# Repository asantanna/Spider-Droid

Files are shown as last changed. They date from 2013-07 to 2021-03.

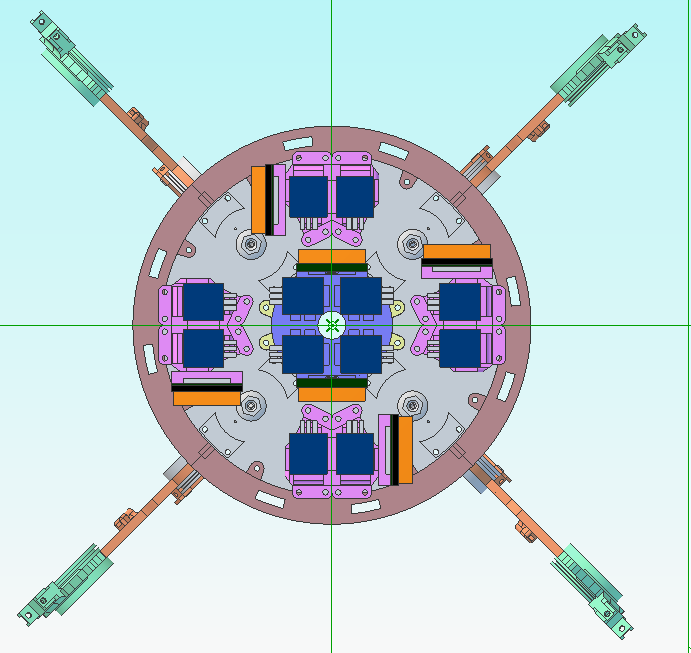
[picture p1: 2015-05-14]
Docs/Raw pics for documents/Phi - Top - Mechanicals Hidden.png

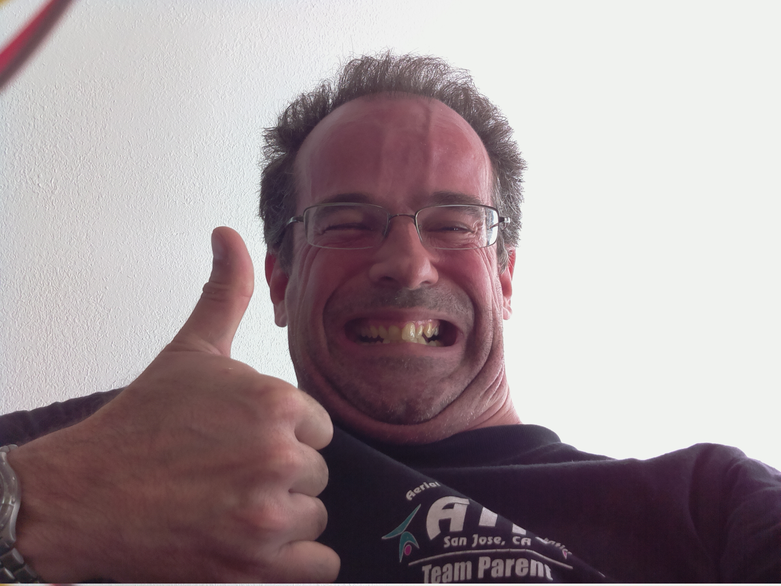
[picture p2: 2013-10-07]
Software/firmware/test/test.jpg

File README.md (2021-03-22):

Spider-Droid
============

Spider like robot - WORK IN PROGRESS

(THIS IS OBSOLETE - COMPLETE RE-IMPLEMENTATION STARTED)

Sparse Checkout
===============

On Raspberry Pi, it is useful to not have to clone this entire repository
since we only need the firmware.  The other stuff will get pretty big and
take up space needlessly.

To set up for this "sparse checkout", create the directory "Spider-Droid"
somewhere on the RPi and copy the file "do-sparse-checkout" into it. (Use
cut & paste or whatever it takes.)

On RPi, look in file for additional instructions.

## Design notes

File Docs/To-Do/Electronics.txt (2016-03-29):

TO DO LIST FOR ELECTRONICS ITEMS
================================

- Aux board does not mount properly on RPi because of video connector clearance
    - remove video connector

- 5V regulator gets very hot
    - install heat sink

- Design touch sensors

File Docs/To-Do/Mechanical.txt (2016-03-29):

TO DO LIST FOR MECHANICAL ITEMS
===============================

BIG AND SMALL SPINDLE:

  DONE *******************- Too much play between spindle and arm, possibly with 
  DONE *******************   spindle and hip limb too

  DONE *******************     INFO: Changes must occur in SPINDLE and BIG SPINDLE to make
  DONE *******************           them thicker.  The alternative, to change the SPINDLE ARM,
  DONE *******************           and RE-MERGE to create SMALL CAP and BIG CAP and the further
  DONE *******************           MERGE to create various other parts is WAY too complicated.

  DONE *******************    SOL: 
  DONE *******************     - Add 0.2 to DIAMETER of hexagon in "SPINDLE" and "BIG SPINDLE"
  DONE *******************     - ignore now incorrect REF sketch in "SPINDLE ARM"

  ******* NOTE *****
  This may make the bearing more snug ... we may need to tweak it back with a revolution "shave"
  if necessary. It's hacky but it's the easiest thing to do BY FAR.

CABLE TUBE SUPPORT:

  DONE ******************* - Need widen hole in cable tube supports
  DONE *******************     SOL: maybe add 0.2 to DIAMETER of hole for glue space too

FRAME:

  DONE *******************- Motor driver support is bad - gap is too thin, holes are two big
  DONE *******************    SOL:
  DONE *******************      - remeasure controller board to see why this happened
  DONE *******************      - change "slot" for driver board to single tabs
  DONE *******************      - figure out what to do about the screws ... I think the holes
  DONE *******************        are too tiny for any of the screws we have.  Try to come up
  DONE *******************        with something clever so we don't need a new screw type.

  DONE ******************* - Need two cable supports for motor wires that go to other frames

  - Need to plan path of motor wires to see where they go and if it will work

  DONE *******************- Paperclip that limits spindle arm is wonky.
  DONE *******************    SOL: 
  DONE *******************      - Add hole to frame to have arm stopper hole go all the way through to other side
  DONE *******************      - Modify stopper hole arrangement so paperclip is more sturdily held in place.
  DONE *******************        (see post-its)

MINI-POT:

  DONE ******************* - Position of threaded hole is incorrect
       *******************   - SOL: fix but must also fix pot base support afterwards

POT BASE SUPPORT:

  DONE ******************* - change to mini-pot invalidates some things
       *******************   - SOL: reproject REF figures, fix hole, fix ridges

=============================================================================

FUTURE
======

- Figure out where RPi, accel, gyro and hip controller attach

- Design touch sensor mechanicals

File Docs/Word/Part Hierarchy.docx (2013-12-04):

Phi Spider Droid Part/Assembly Hierarchy:

(A) = Assembly
(P) = Part

- Phi (A)
  - Head (A)
    - Head Dome (P)
    - Gyroscope (P)
    - On/Off Switch (P)
    - Battery (P)
    - LEDs (P)
  - Main (A)
    - Logic Unit (A)
      - Board Mount (P)
      - Raspberry Pi (P)
      - Phi Logic (P)
    - Hip Unit (A)
      - Hip Motor Mount (P)
      - Pot Mount (P)
      - Hip Motor (P) x 4
      - Pulley x 4 (P)
    - Leg Frame (P) x 4
    - Leg Unit (A) x 4
      - Leg Control (A)
        - Motor Mount (P)
        - Pot Mount (P)
        - Bearing Mount (P)
        - Motor Controller (P)
        - Motor (P) x 2
        - Pot (P) x 2
      - Leg (A)
        - Hip (P)
        - Thigh (P)
        - Shin (P)
      - Pulley – Thigh (P)
      - Pulley – Shin (P)
  - Skirt (P)

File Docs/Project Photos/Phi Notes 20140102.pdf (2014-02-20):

## PHI Project Notes

Overview

The name of the robot is PHI because, as everybody knows, Greek letters are COOL.

It is loosely based on the Star Wars Spider Droid. Loosely because after close inspection, I concluded it wouldnt work There are linkages missing, etc unless they use light saber technology or something.

Software

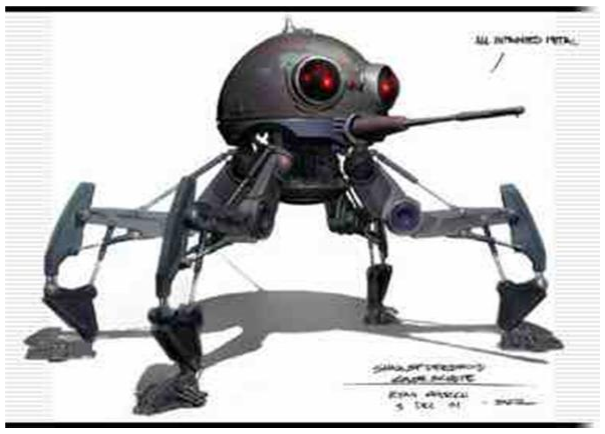
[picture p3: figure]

The software is broken into two parts:

1) Firmware (on robot)
a. Hardware Control (sensors and effectors)
b. Web server for diagnostics
c. PhiLink (50 fps telemetry link)
2) Phi Core (on Windows PC)
a. Remote brain for robot robot is teleoperated like a puppet through PhiLink. At this point it is mostly WISHFUL THINKING. Only diagnostics and telemetry work.
b. Self-programmed guided by hardwired instincts and goals
i. Instincts are things I presume comes wired in out of the egg. Things like pleasure seeking, pain aversion, curiosity, investigation, prediction, play, feeling in control, etc
ii. Goals are loose good/bad indicators that guide learning. Similar to instincts but less fuzzy. E.g. at a very low level, a goal of the low joint sensor/motor subsystem is to explore the causality between motor commands and joint movements. This is how Phi learns it has a leg.
iii. Self-programming is based on various information-theoretic goals. 1. Maximal communication entropy between systems (ie best channel

utilization)
2. Maximal PIG (predicted information gain). This means that exploration actions are selected on the basis of filling in missing knowledge relevant to the goal.
3. Best compression between sensor and memory by the information bottleneck method. Lots of data from sensors but very little is relevant to a particular subsystem. Subsystems compress (and discard) data that is not relevant to its goal. In other words, information goes through a bottleneck.

Hardware

Quick summary:

- Raspberry Pi single board computer running Raspbian Linux (derived from Debian) - Auxiliary custom PCB for: Voltage regulators , Analog-to-Digital converters, SPI and I2C bus

expanders, etc. - 12 gear motors (35:1 ratio), 3 per leg

- 6 motor controllers (one can handle 2 motors) - 12 Potentiometer based joint position sensors, 3 per leg
- 4 touch sensors on feet
- Static Accelerometer senses acceleration on 3 axes. Good for detecting translational movement of robot
- Digital Gyroscope senses rotational acceleration around 3 axes. Good for detecting robot rotations. - 50 fps HD camera (resolution will probably be reduced significantly to keep frame rate up) - 2400 mAh 9V batteries
- 9V for motors
- 5V for Raspberry Pi
- 3.3V for assorted logic
- On/off switches and assorted blinkenlights

Plastic

View of one Quadrant of robot. Phi is made of four of these, a head dome and an undercarriage dome.

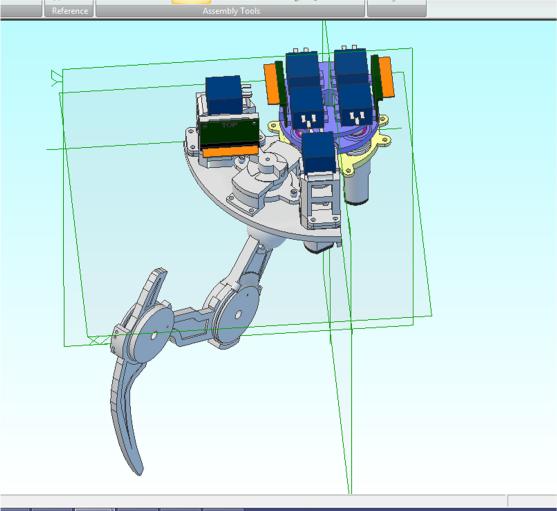
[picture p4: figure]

Side view of a Quadrant:

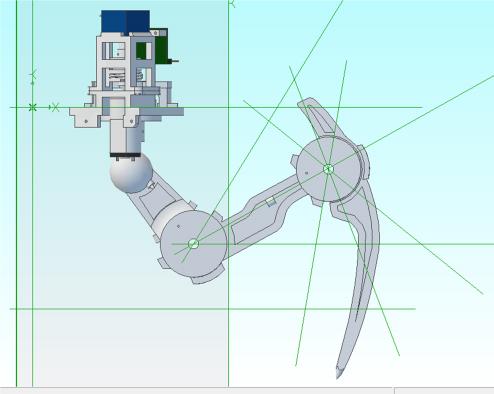
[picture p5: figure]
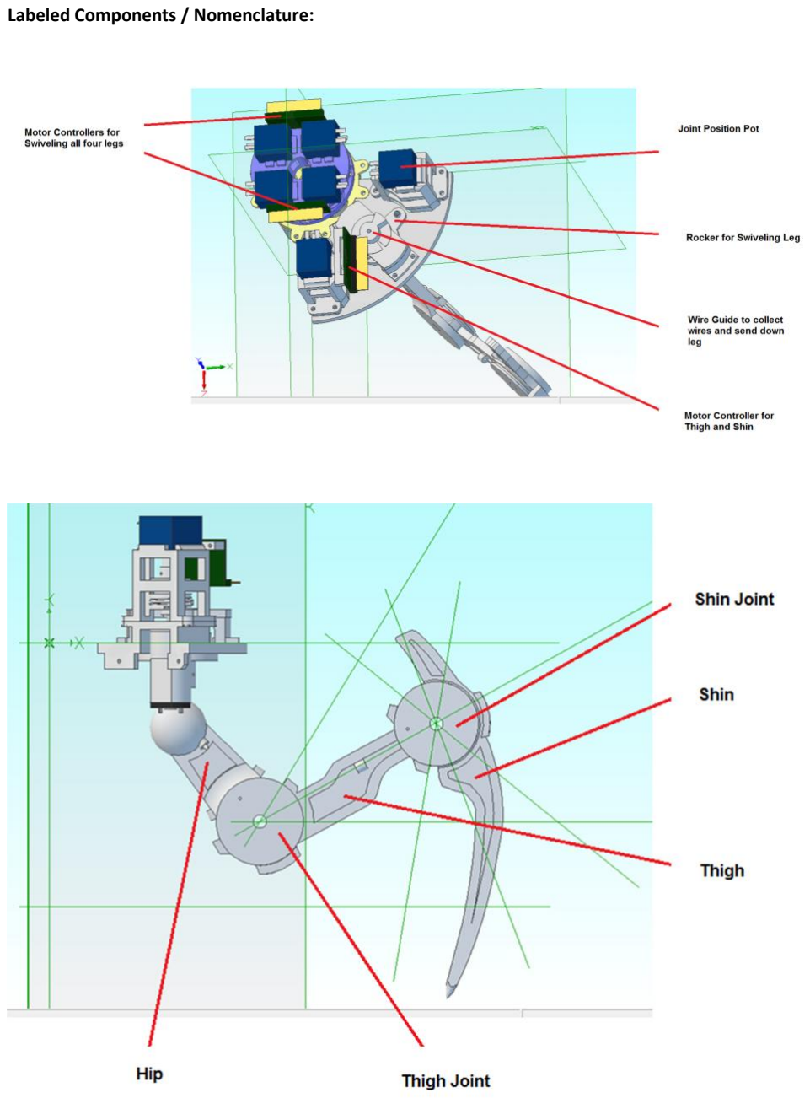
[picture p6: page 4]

Labeled Components / Nomenclature:

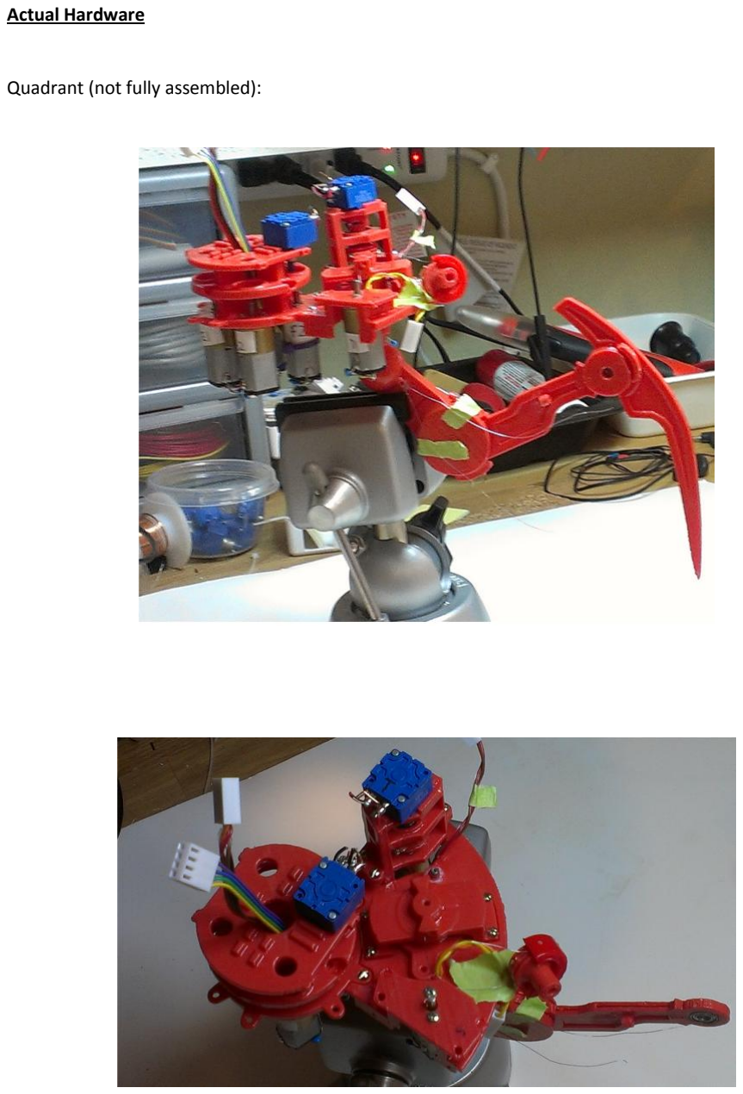
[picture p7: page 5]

Actual Hardware

Quadrant (not fully assembled):

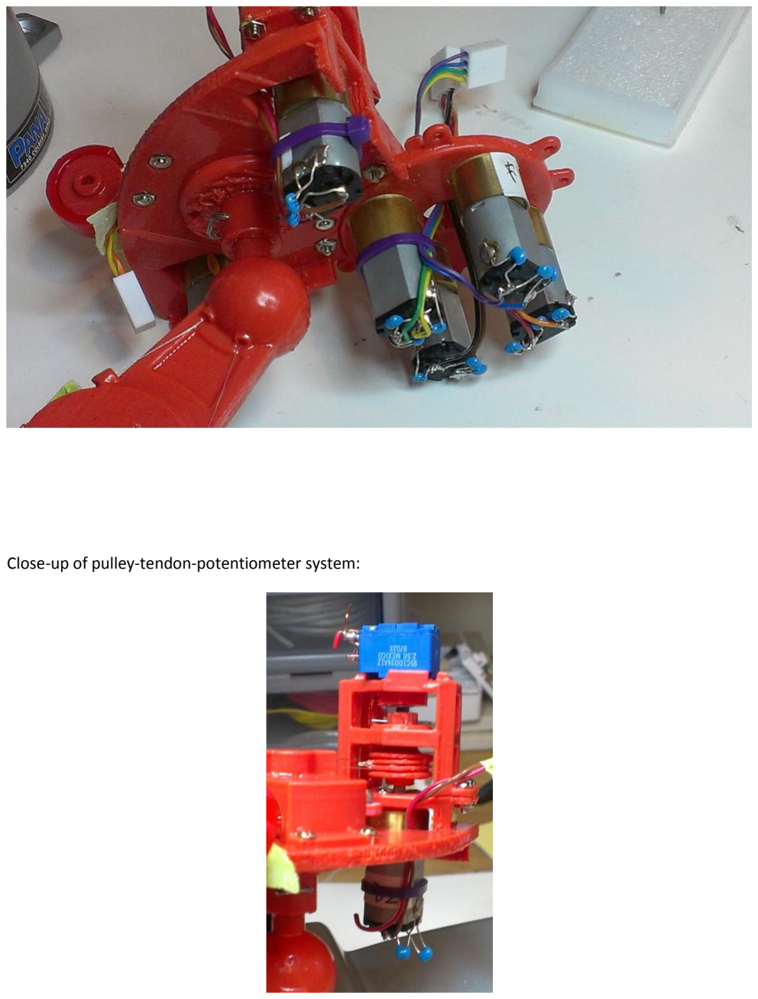
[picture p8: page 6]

Close-up of pulley-tendon-potentiometer system:

Aux Board

Top:

Bottom:

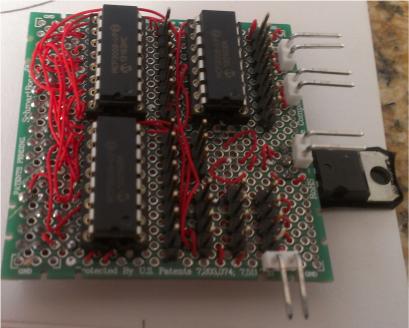
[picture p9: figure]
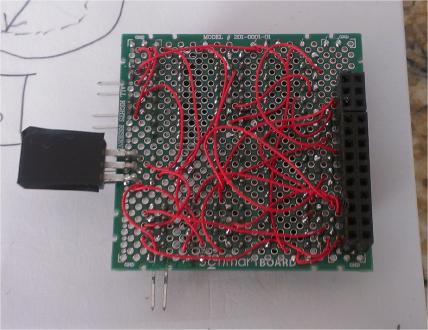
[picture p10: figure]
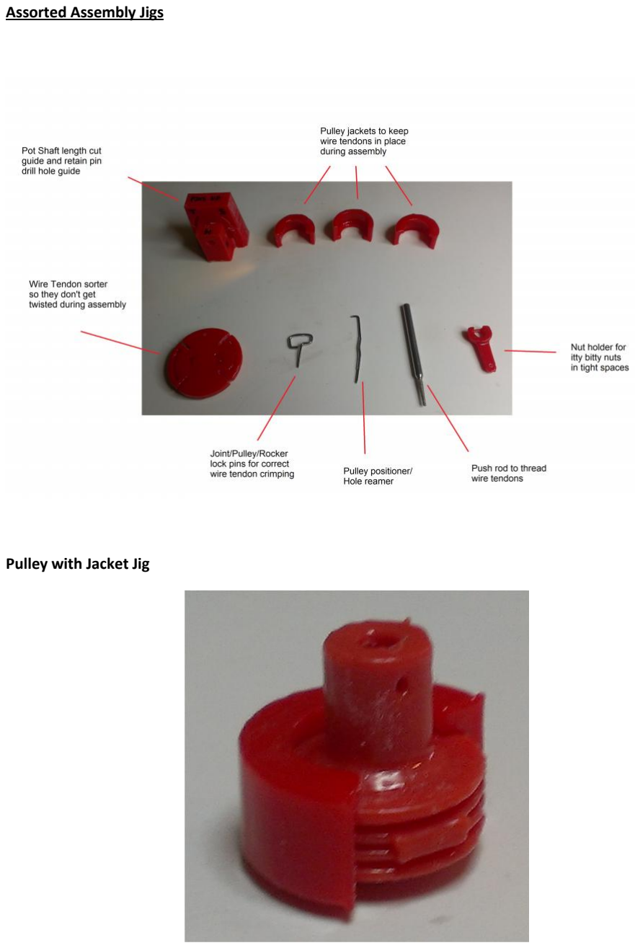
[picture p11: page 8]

Assorted Assembly Jigs

Pulley with Jacket Jig

Most Important

Project Mascot (weird Egyptian God)

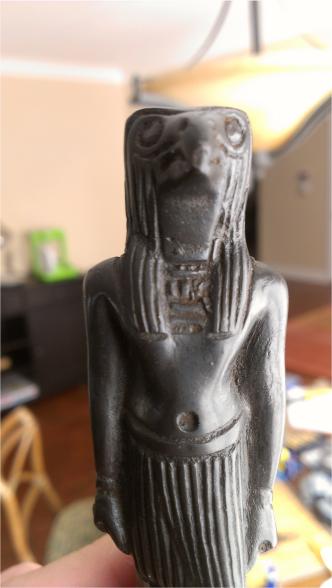
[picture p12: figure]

Keychain (no mugs or T-shirts yet)

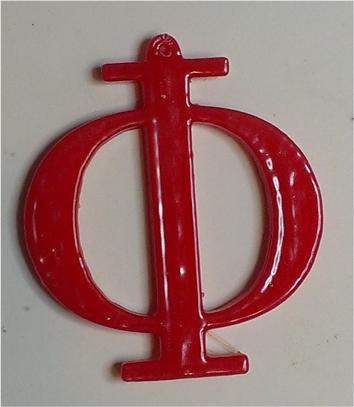
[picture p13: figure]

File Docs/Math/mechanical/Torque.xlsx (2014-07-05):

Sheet: Calculations
Motor Torque Calculations |  |  | * see note 1
 | Motor Type: | Polulu 1598 | g / oz | 28.35
 | Gear Ratio: | 115 : 1 | mm / in | 25.40
 | Stall Torque (oz-in) | 35.00 | Pulley Rotation (turns) | 0.75
Inputs | Motor Pulley Radius (mm) | 6.50 | * see note 2
 | Joint Pulley Radius (mm) | 15.00 | * see note 3
 | Limb Length (mm) | 76.42 | * see note 4
Intermediate | Stall Torque (gf-mm) | 25202.71 | Mot Pulley Circum (mm) | 40.84 | hypothenuse (mm) | 15.00
 | Wire Tension (gf) | 3877.34 | Wire Travel (mm) | 30.63 | base (mm) | 15.32
 | Leg Torque (gf-mm) | 58160.09 | Attach Pt Circum (mm) | 94.25
Results | Endpoint Force (gmf) | 761.08
 | Wrap Leg Rotation (deg) | 117.00 | if attached like a pulley (wrapping)
 | Lever Leg Rotation (deg) | #NUM! | if attached to a lever (with symmetric movement)
Design Decisions | THIGH |  | SHIN
 | Motor Pulley Radius (mm) | 6.50 | Motor Pulley Radius (mm) | 6.50
 | Joint Pulley Radius (mm) | 30.00 | Joint Pulley Radius (mm) | 29.00
 | Limb Length (mm) | 76.42 | Limb Length (mm) | 103.93
 | Wrap Leg Rotation (deg) | 58.50 | Wrap Leg Rotation (deg) | 60.52
 | Endpoint Force (gmf) | 565.37 | Endpoint Force (gmf) | 401.86
Notes:
1) This worksheet computes a *single* joint at a time. The Design decisions at bottom are cut/paste of values for different joints.
2) The motor pulley radius is self-explanatory.
3) The joint pulley radius is equivalent to the radius of the "other" pulley - the one at the joint. When there is no pulley, just a lever arm like the hip rocker, it is the length of the arm.
4) The limb length is the length of the limb being moved. This length is the joint-to-joint straight distance. For the thigh, it is the distance between bearing centers. For the shin, it is the distance from the center of the bearing to the contact point.

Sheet: Polulu Motor Data
Motor Type: | Polulu 1795
Gear Ratio: | 35 : 1
Stall Torque (oz-in) | 13.00
Motor Type: | Polulu 1598
Gear Ratio: | 115 : 1
Stall Torque (oz-in) | 35.00

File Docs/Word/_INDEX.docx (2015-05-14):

PHI Index

Mind/Memory Hierarchy

Concepts

Noise

States & Change

Mind/Memory Hierarchy

It seems reasonable that:

- Big concepts are built of smaller ones.
- Information is not endlessly repeated so the same datum/concept is not duplicated in every concept/memory that refers to it. In other words, concepts are referenced with something like pointers.

However, this leads to several consequences:

- If a concept changes, then anything referencing it will also change.
- If the change is small, perhaps this does not have great consequences.
- If , however, the change in the concept is big, or if it becomes invalid, then the concepts/memories that reference it either become incorrect or end up having what is in effect a dangling pointer – ie a reference to a no longer existent concept.
- We can think of the concept hierarchy as a building where “foundation concepts” form the base and new concepts are built on top. Modifying the base can cause large quakes in the whole structure.

Is this reflected in what we know about memory development?

When the system has very little experience, there isn’t much that already exists and can be properly considered to be foundational data. This means that structures built are quite likely to be built incorrectly (strange/useless concepts, weird/crazy causality, overly convoluted organizations, very little generalization, etc.) and that these “uneducated” systems will inevitably be subjected to deep revisions as time goes by and “refereeing data” invalidates previous concepts.

This is inevitable:

1) A core of experience must be acquired in order to properly create/organize concepts correctly/usefully. In the beginning, there will not be enough history to do so and things will very likely be messy.
2) Since concepts are continually being built on other concepts and memories are continually being built referring to whatever concepts we currently have on hand, a structure with shaky foundations will be built at first.

Concrete Consequences:

Since the less experience a system has, the more malleable are its foundations, then “younger” systems will not be able to “remember” as far back as a more experienced system. The concepts that form memories in young systems will get invalidated much more often and these memories will cease to make as much sense. When the concept changes are small, the invalidated concepts might cause only a fuzzy memory to remain. When the change is big, the memory might be sufficiently damaged so as to make it terminally invalidated. These probably get discarded or simply wither away through some auxiliary mechanism.

This also provides a more palatable alternative to the idea that we have hardwired phases of development such as strict hardwired learning windows. Instead:

1) We would explain the beginning of a learning window as the (fuzzy) point in time where a sufficiently reliable foundation exists on which to build a particular type of concept. Before this point, either the necessary base concepts do not exist or are in flux, preventing the formation of a solid and persistent new concept.
2) Similarly, the end of a learning phase is not “genetically preprogrammed” but is instead a consequence of the foundations firming up as its concepts become more established and entrenched through verification. Presumably a mechanism exists where a heavily verified and/or relied upon concept is not easily changed as something that is new and/or untried.

Anecdotal Evidence:

1) By observing young children, 8 year-olds, 12-year olds, etc. It is readily apparent that they have *very* good memories. There is nothing wrong with their ability to form memories that are precise and robust. Yet, we know that the great majority of these memories will be lost as they grow older. None of us remember much from those years and when we do, not with any great clarity.  This explanation proposes that what happens is that most memories become terminally invalidated and subsequently lost. Memories of deep emotionally significance, for example, might, on the other hand, still retain enough “pointers” to valid base foundational concepts (the emotions themselves) so as to survive – but with likely great lack of clarity since other components of the memory will probably have been invalidated. Potentially, these heavily compromised components are then repaired by the mind by either:
  a. Automatic repair / confabulation (which appears to be rigidly controlled, except when the mind is subjected to very peculiar circumstances such as separated hemispheres or some types of disease or damage)
  b. Conscious replacement / rationalization of what “ought to be there” or “was told was there”
2) In contrast, with older people, we do not see this widespread “wiping out” of whole periods of memory. It is quite common for even very old people to say “they remember that as if it was yesterday” even when referring to events that occurred many decades ago. This explanation proposes that for older people, very large and time tested hierarchies exist at the time of memory formation and that they consequently do not require deep revisions afterwards. Thus the memory is preserved with great clarity.
3) It should be said that this doesn’t mean that older, more experienced people will therefore remember everything. Instead, what is being said is that if other mechanisms mark a memory as worth remembering, it will last longer and retain greater clarity for these more experienced people due to the stability of their mental hierarchy. (We are of course referring to healthy people – at advanced ages, senility may cause the system to malfunction in a variety of ways – in both memory formation and retrieval.)

Consequences to Phi

1) To get the ball rolling, there should probably be some hardwired foundational concepts.
  a. Simple feelings and emotions seem intuitive: pain, hunger, fear, etc.
  b. Maybe all qualia are foundational concepts. However, when we think of color for example, it seems clear that color qualia are not fully hardwired but instead develop over time (but probably very early). Consider that an animal that is born with a mutation that endows it with a new photo-pigment would develop qualia to represent the new colors. Since this happens often throughout evolution with success – it seems that the qualia cannot be fully hardwired because it would be extremely unlikely to have both the mutation for the photo-pigment and a suitable mutation to the hardwiring occurring at the same time.
2) Suitable mathematical mechanisms must be devised to:
  a. Form concepts.
  b. Evaluate the trustworthiness (though validation) and authority (through being relied upon) of concepts
  c. Controlling the ease of modification/invalidation of concepts. (Can concepts be modified or only invalidated and replaced? Or both?)
  d. Recovering from such invalidations both in the concept hierarchy and in memories.

Concepts

It seems intuitive that concepts must be some sort of (exclusive?) categorization of the state and that any concept cannot be always active.

1) If two concepts are indistinguishable, they are logically the same concept
2) If a concept is always active, then it is not useful to base a decision. So concepts must be active only part of the time.
3) Similarly, if a concept is never active, again it is useless.

Concepts and info theory:

1) It follows from the above that with concepts, some sort of information entropy argument should apply. Ideally there should be an equal distribution of the activity of concepts or something.
2) Also, since concepts are categorizations of state, we are often interested in cause and effect between them.
3) This is a bit confusing – if a concept is a categorization of state then it might also be a cause? In which case it’s hard to argue for entropy. For example, if a concept can be a cause and a particular cause might be an event that happens once and has big consequences and should be remembered. This does not seem to have anything to do with entropy.
4) Maybe we need to say something like causes are identified by co-occurrence of concepts. The concepts need to follow entropy arguments – the causes are just episodic memories of cause coincidences?

Noise

With regards to states and concepts, we are always most interested in transitions (changes) between them. The problem is that noise can cause random transitions that cannot be solved by simple discretization.

1) Even with states being categories that are discretized far apart, if the true state of the system is on the border between categories, noise can make them appear to ping-pong back and forth.
2) A mechanism is required to prevent this ping-ponging such as:
  a. Some type of Hysteresis
  b. Some sort of momentum mechanism that keeps the state moving into the new symbol and thus away from the border
  c. Having a “no-man’s land” between states and having a mechanism that generates change events only if the transition is part of a sequence of the form. If the no-man’s land is wide enough, noise will not be able to fully traverse it on its own to enter a new symbol and thus will eventually reenter the same symbol – causing the change to be ignored.

States & Change

1) Changes are the fundamental entities from which any intelligent system is built since, ultimately, only changes can be used to trigger decisions and thus actions (physical or mental) that the system predicts will be beneficial. This follows from the logic that:
  a. If an action is to occur, it must perforce have a cause or decision preceding it to trigger it to begin.
  b. This trigger must occur at a specific moment to have beneficial results.
  c. A “moment” can only be identified if it is different from the moment immediately preceding it in some way.
  d. Thus the change that allows identifying the beginning of a specific moment is THE fundamental entity from which intelligent systems are built.
2) States on the other hand, are related to changes because we can say that a transition from one state to another is what constitutes the change.

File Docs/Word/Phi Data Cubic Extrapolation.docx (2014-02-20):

Phi Data Cubic Extrapolation

A common method for extrapolating (or interpolating) data points is cubic interpolation/extrapolation. Interpolating is when you want to guess a point between some other data points. Extrapolating is when you want to guess a point outside other data points.

Interpolation: Extrapolation:

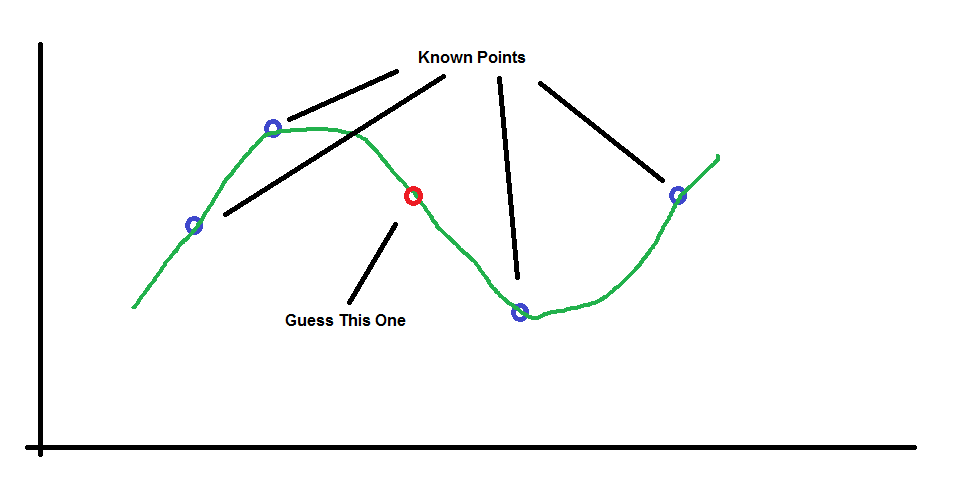
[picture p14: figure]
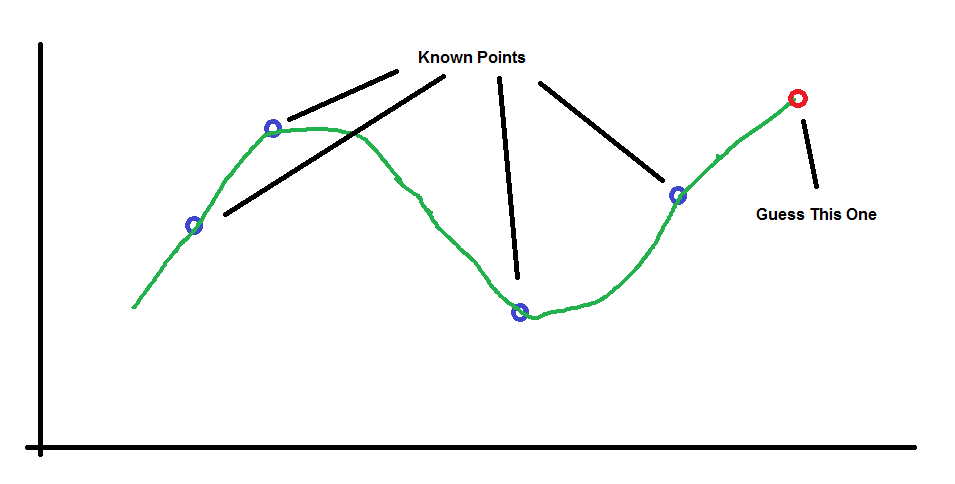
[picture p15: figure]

The problem is that we don’t know the green curves beforehand so it’s actually impossible. However, if we assume a few things that are not too unreasonable, then the problem becomes solvable. We will assume 2 things:

1) The curve is smooth looking – not some crazy hairball type of thing
2) It has at most 2 “bends” – places where it changes direction. In other words, at most 2 reversals from “increasing” to “decreasing” (or vice versa).

A family of curves that meets our requirements is described by what is called a cubic equation. The idea is that we will provide some existing points and assume that they are on a curve that can be described with a cubic equation and ask: “if we know all these points are on a cubic curve, then what is the equation of the curve?”

The general form for any cubic equation is:

Our goal is to determine what the values of a, b, c and d using some example points that we claim are on the cubic equation we want to know. Since we want to solve for 4 values, there’s a mathematical rule that says we need 4 “examples” in order to figure it out. (It will become clear why this is so below.)

So the example points will be:

Thus there are four equations that must be true:

We want to solve for a, b, c and d in general but there is a trick that we can use to make things simpler. The reason we want to solve the cubic equation is because we want to guess a point at some other x value such as x5, but if we shift the points left or right to make sure that the point we want to guess is always at 0, then all we need to solve for is d; the equation for the point we want would then be :

Here’s how to solve it. First solve for a in terms of the others using the first equation:

Matlab answer:

2

b x1 + c x1 + d - y1

3

x1

Now, use this value for a in the second equation to make a go away. Then solve for b.

Matlab answer:

The value of b is:

3

x2 (d - y1 + c x1)

d - y2 + c x2 - -------------------

3

x1

3

x2 2

--- - x2

x1

Now solve for c using the 3rd equation:

Got tired of simplifying … stopped doing it here.

Matlab answer:

The value of c is:

2 2

x2 x3 (y1 - y3) x2 x3 (y1 - y2) x2 x3 (d - y1) (x2 - x3)

2 2 2 2 ---------------- - ---------------- + ------------------------

d x2 - d x3 - x2 y3 + x3 y2 x1 - x3 x1 - x2 x1

2 2 x2 x3 (x2 - x3)

x2 x3 - x2 x3

And FINALLY!!! :

Lucas and I didn’t want to spend the next six hours doing this so we just gave it to Matlab.

Matlab answer:

The value of d is:

2 2 2 2 2 2

- y4 x2 x3 + y3 x2 x4 + y4 x2 x3 - y3 x2 x4 - y2 x3 x4 + y2 x3 x4

2 2 2 2 2 2

- x2 x3 + x2 x4 + x2 x3 - x2 x4 - x3 x4 + x3 x4

x2 x3 x4 (x3 - x4) (y1 - y2) x2 x3 x4 (x2 - x4) (y1 - y3) x2 x3 x4 (x2 - x3) (y1 - y4)

---------------------------- - ---------------------------- + ----------------------------

x1 - x2 x1 - x3 x1 - x4

(x2 - x3) (x2 - x4) (x3 - x4)

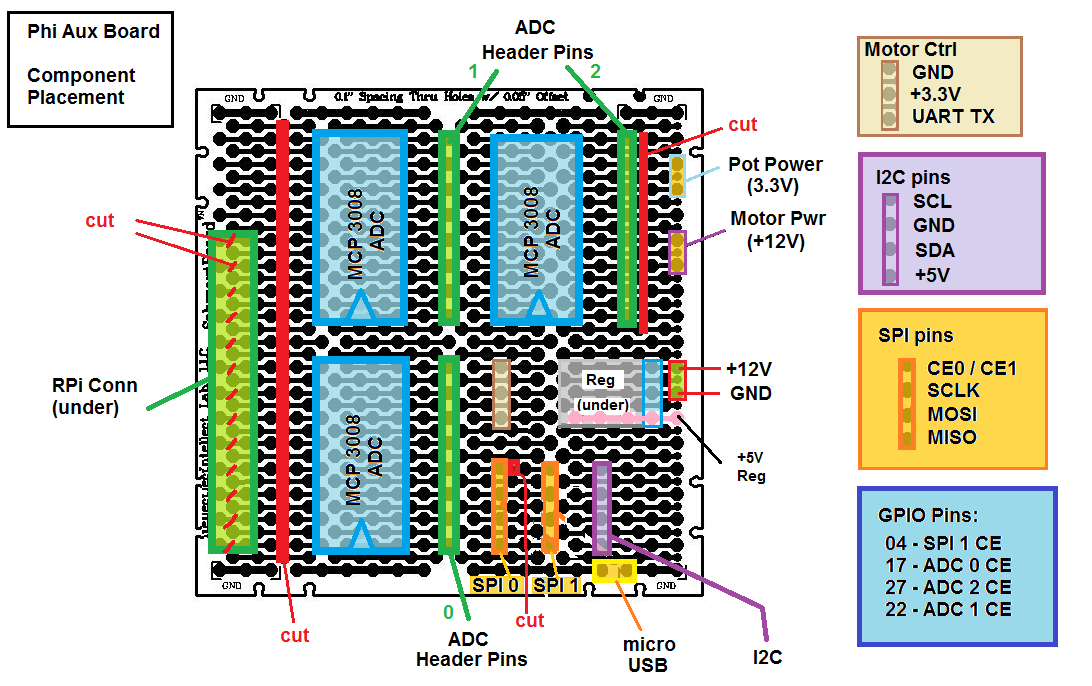
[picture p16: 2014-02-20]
Phi Schematics/Prototype Board/schmart-board-placement.png

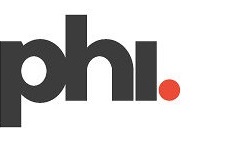
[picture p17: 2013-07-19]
Software/firmware/bin/wwwRoot/images/phi_text.jpg

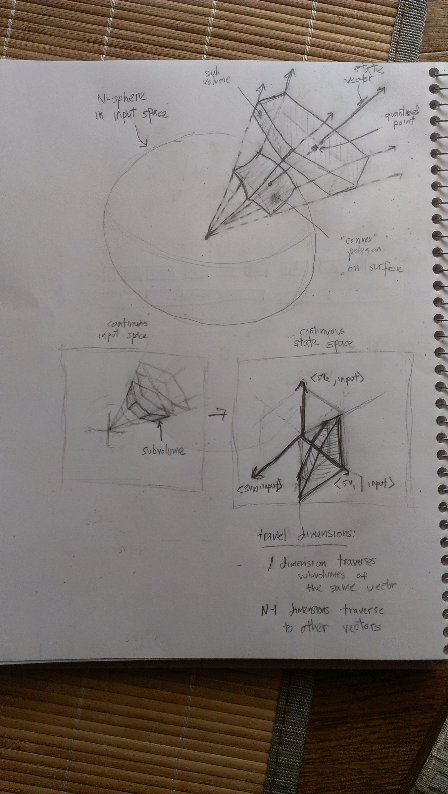
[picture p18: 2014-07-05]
Docs/Raw pics for documents/State spaces.jpg

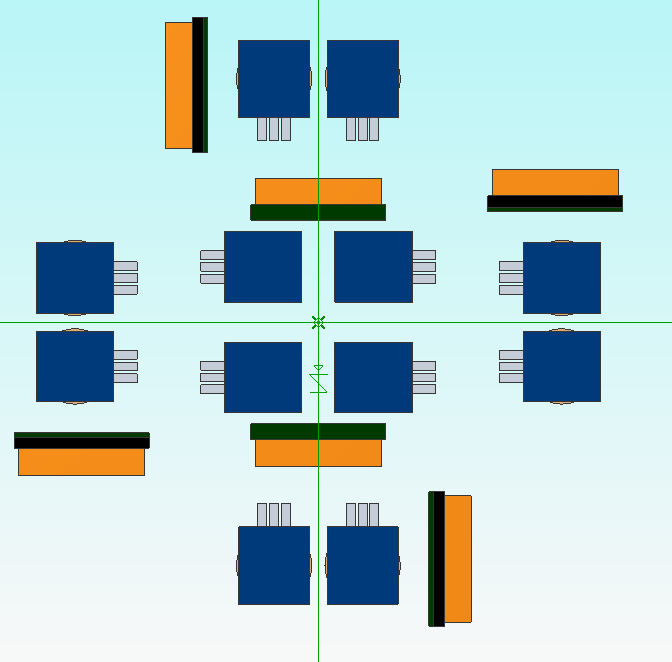
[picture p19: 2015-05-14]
Docs/Raw pics for documents/Phi - Top - Pots & Controllers Only.png

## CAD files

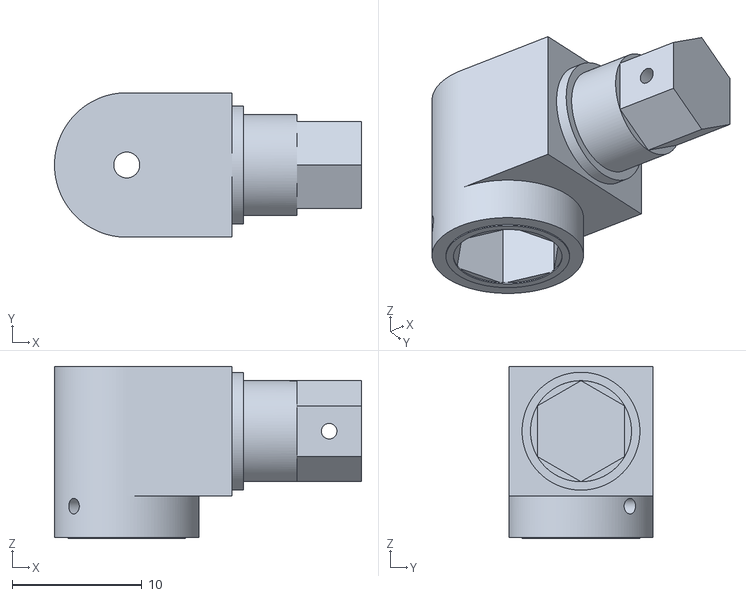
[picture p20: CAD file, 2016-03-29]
GeoMagic/Version 0.3 - Abandoned/STL Files/MERGED - Thigh Arm R.stl
23.7 x 11.2 x 13.3

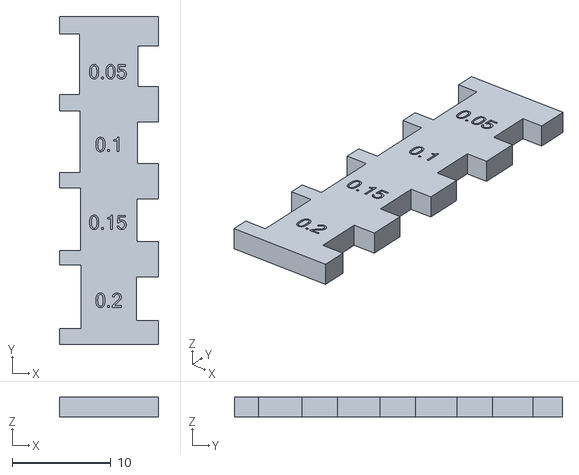
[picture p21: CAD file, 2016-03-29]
GeoMagic/Version 0.4/STL Files/Clearance Notches.stl
10.0 x 33.2 x 2.00

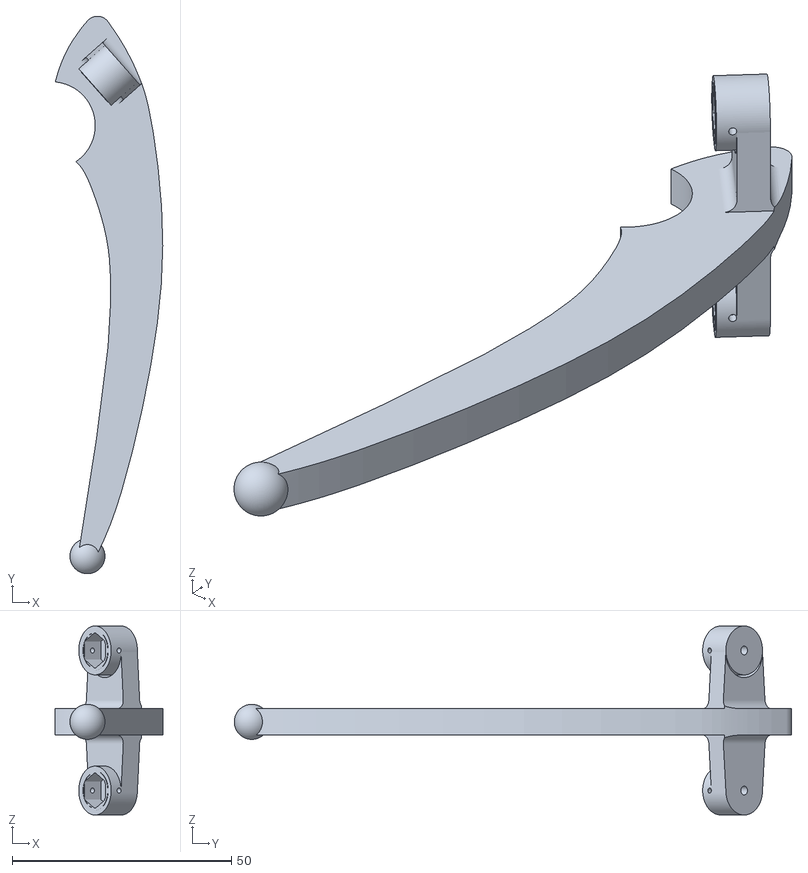
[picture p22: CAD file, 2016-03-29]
GeoMagic/Version 0.3 - Abandoned/STL Files/MERGED - Shin Limb.stl
24.5 x 127.2 x 43.1

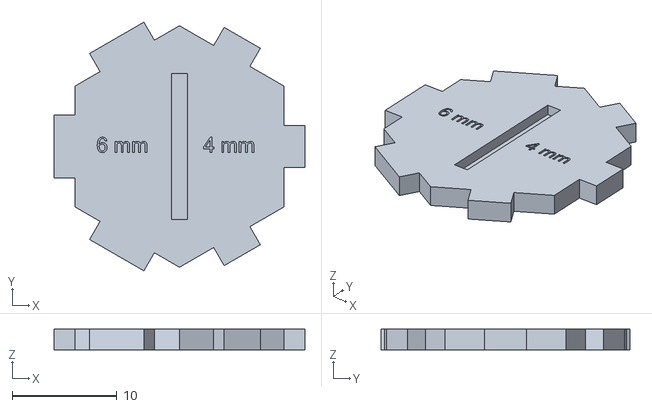
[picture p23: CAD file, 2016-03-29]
GeoMagic/Version 0.4/STL Files/Clearance Notches B.stl
24.0 x 23.8 x 2.00

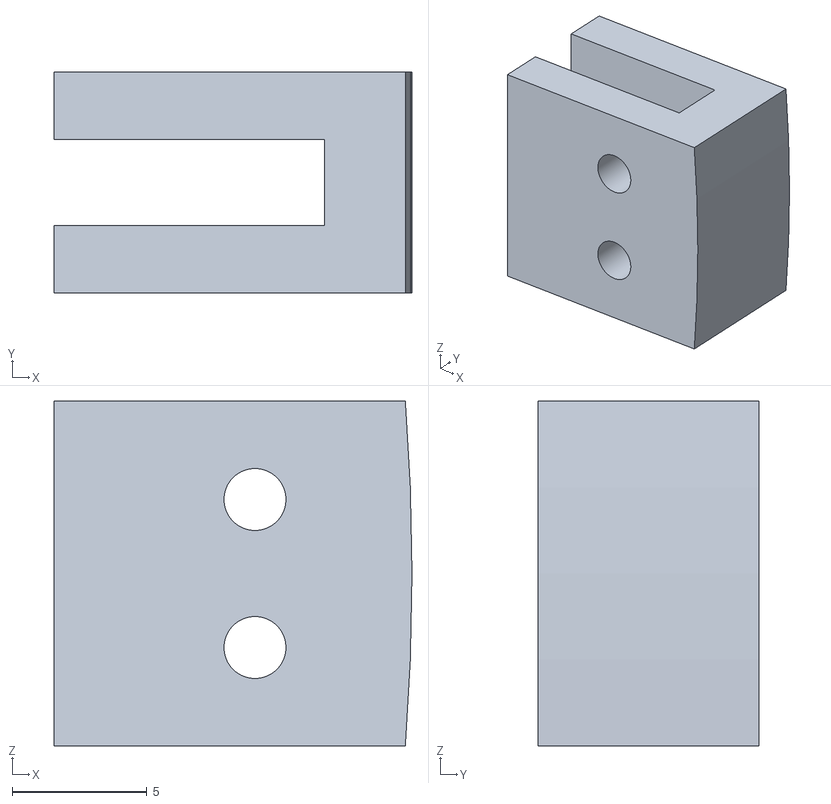
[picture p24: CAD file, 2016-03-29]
GeoMagic/Version 0.3 - Abandoned/STL Files/Outer Frame Clip.stl
13.3 x 8.20 x 12.8

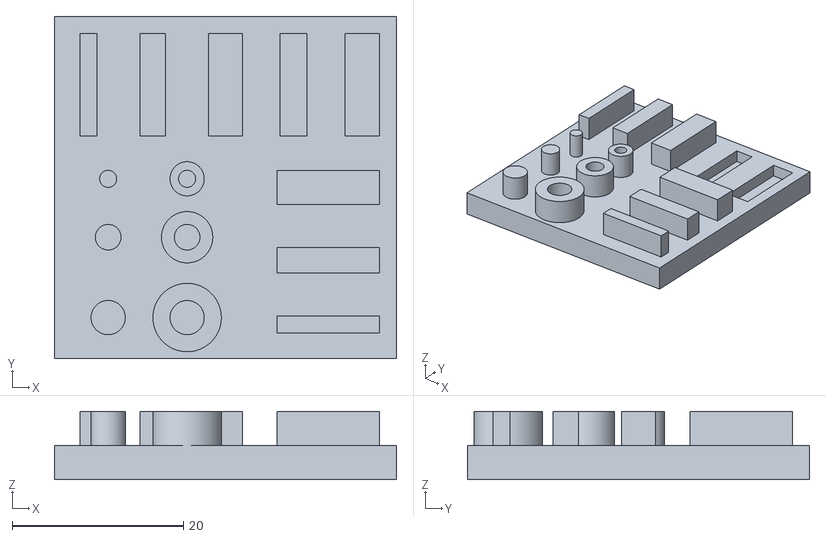
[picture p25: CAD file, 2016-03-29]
GeoMagic/Version 0.4/STL Files/Lines and Circles Calib.stl
40.0 x 40.0 x 8.00

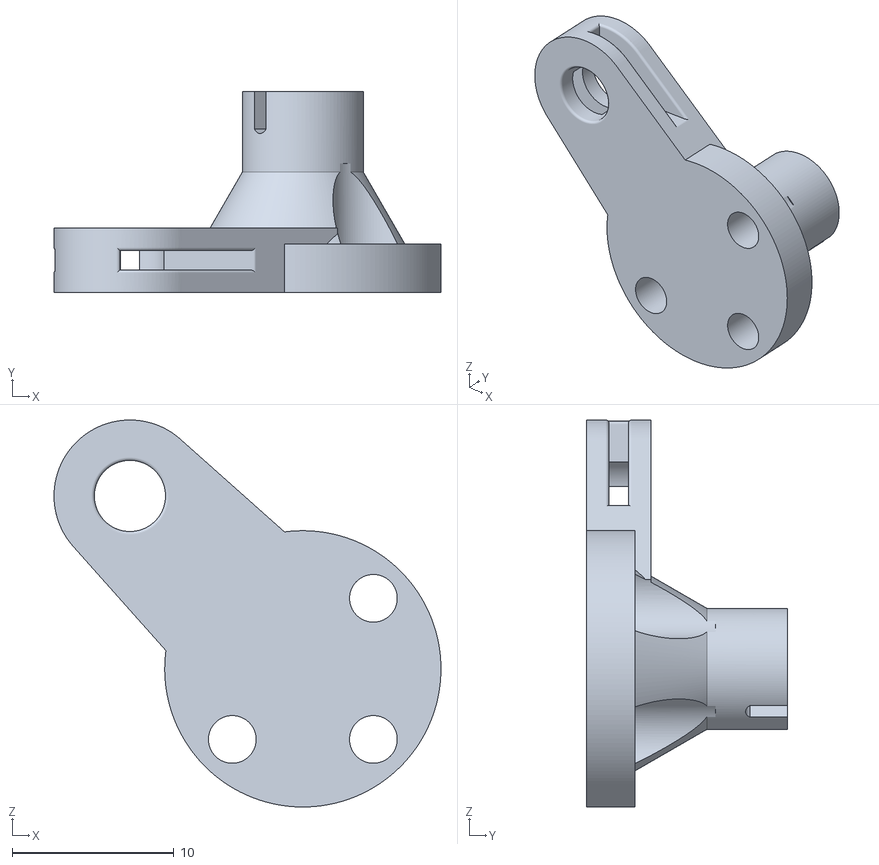
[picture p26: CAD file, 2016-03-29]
GeoMagic/Version 0.3 - Abandoned/STL Files/MERGED - Hub Arm.stl
23.9 x 12.4 x 23.9

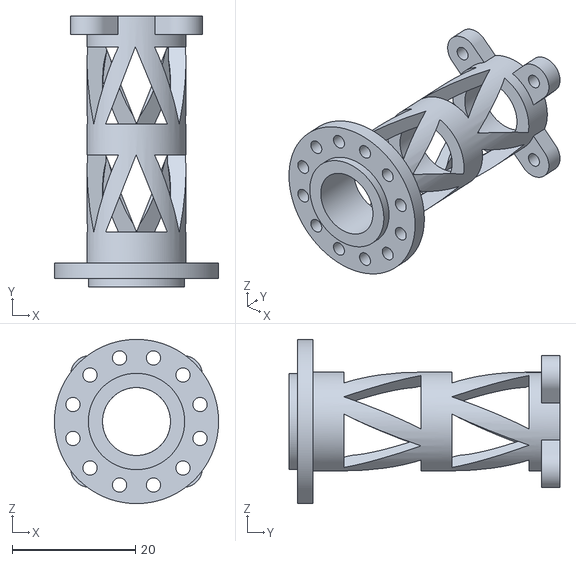
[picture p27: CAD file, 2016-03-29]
GeoMagic/Version 0.3 - Abandoned/STL Files/Tower.stl
26.6 x 43.9 x 26.6

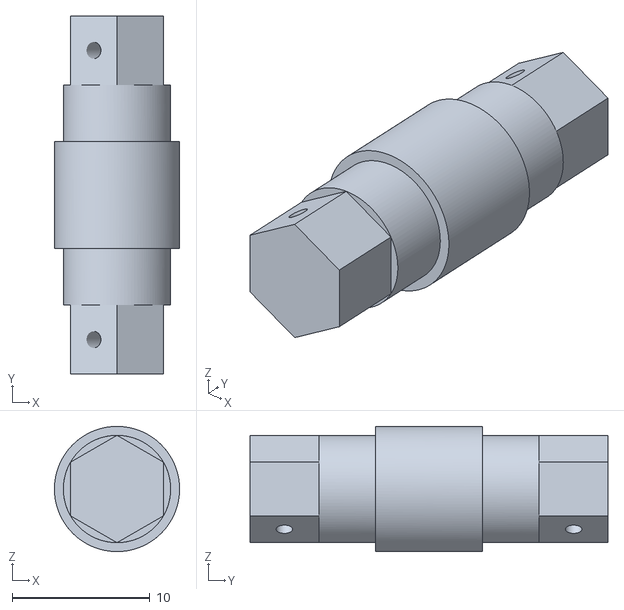
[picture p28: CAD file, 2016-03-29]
GeoMagic/Version 0.3 - Abandoned/STL Files/MERGED - Thigh Spindle.stl
9.10 x 26.0 x 9.10

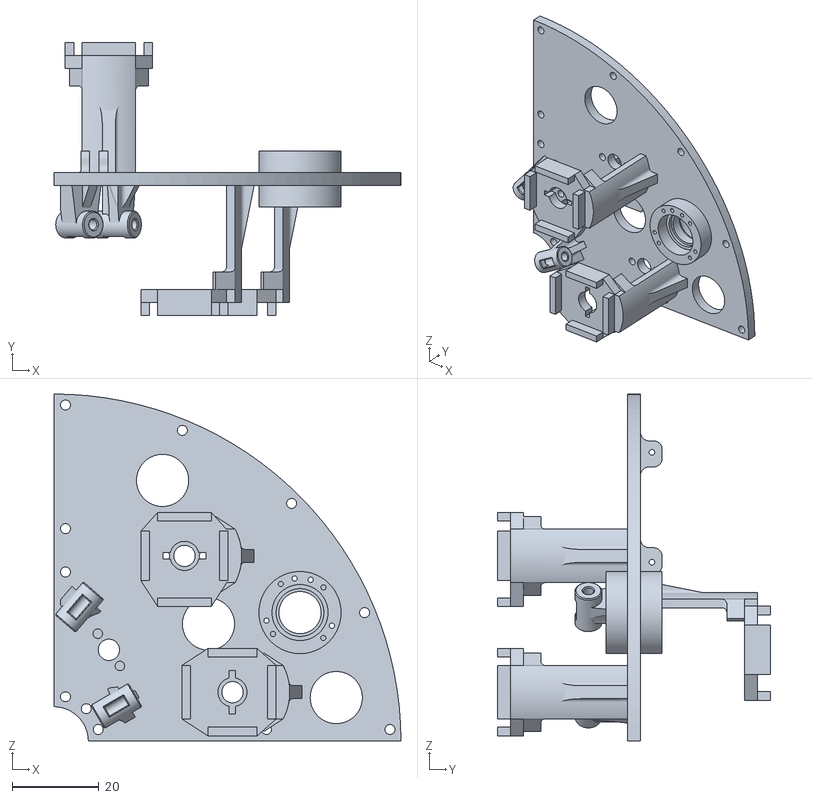
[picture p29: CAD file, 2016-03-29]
GeoMagic/Version 0.3 - Abandoned/STL Files/MERGED - Frame A.stl
79.9 x 62.9 x 79.9

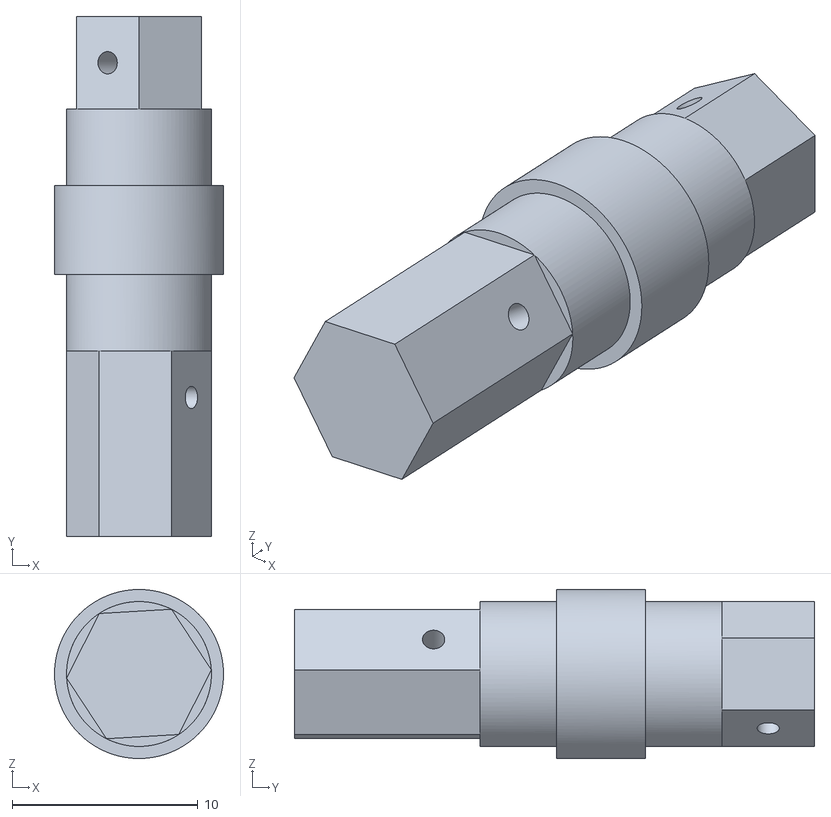
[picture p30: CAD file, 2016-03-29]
GeoMagic/Version 0.3 - Abandoned/STL Files/MERGED - Spindle for Frame A.stl
9.10 x 28.0 x 9.10

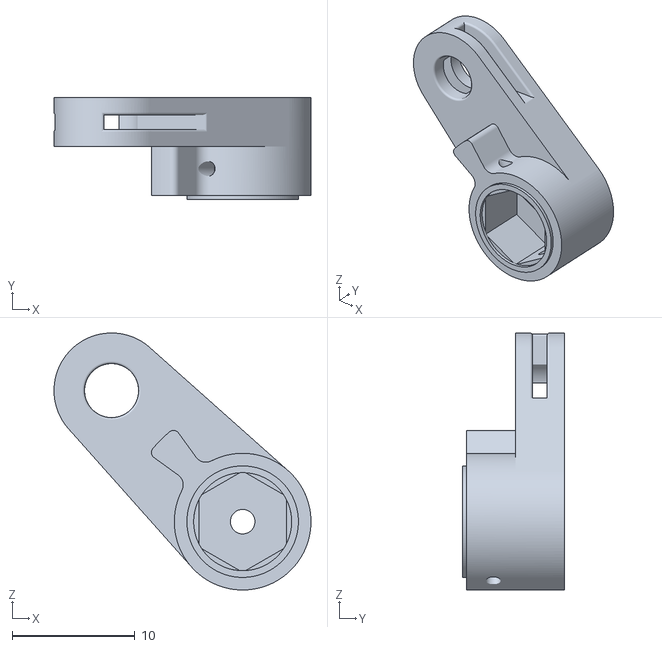
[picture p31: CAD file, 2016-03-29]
GeoMagic/Version 0.3 - Abandoned/STL Files/Spindle Arm.stl
21.0 x 8.30 x 21.0

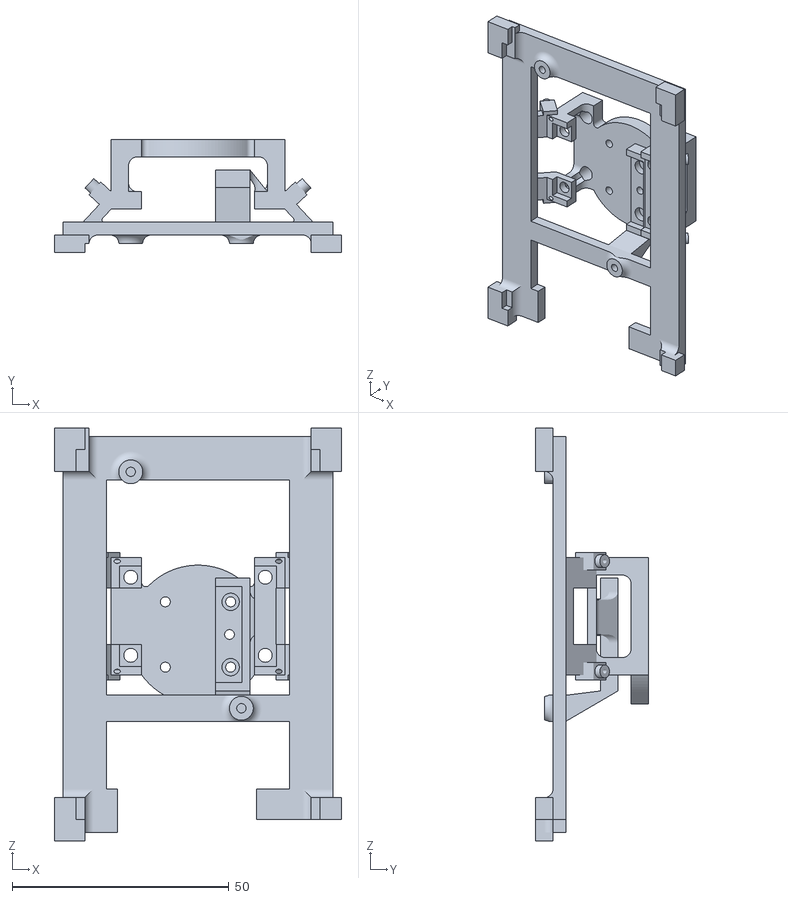
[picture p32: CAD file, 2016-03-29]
GeoMagic/Version 0.3 - Abandoned/STL Files/RPi Support.stl
66.2 x 26.0 x 95.2

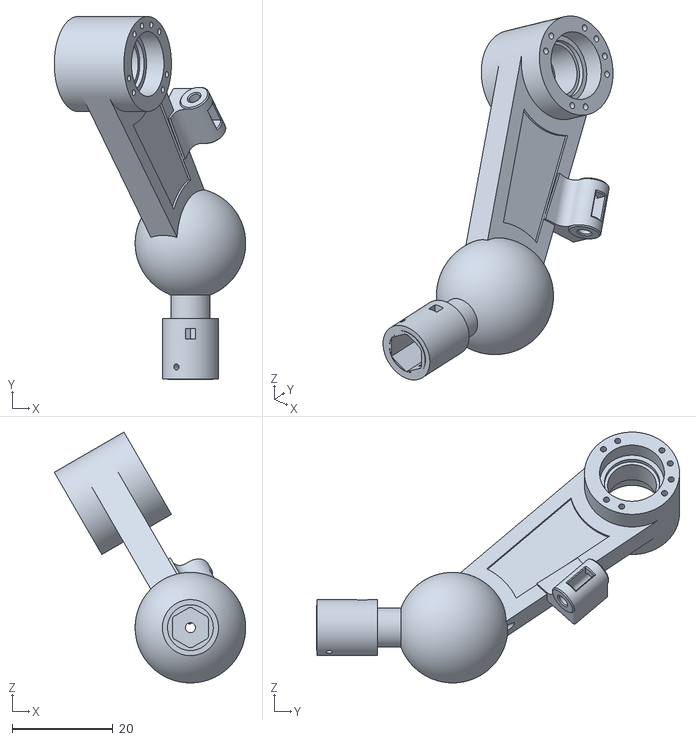
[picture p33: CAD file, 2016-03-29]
GeoMagic/Version 0.3 - Abandoned/STL Files/MERGED - Hip Limb.stl
38.1 x 72.2 x 49.9

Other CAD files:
GeoMagic/Version 0.3 - Abandoned/STL Files/MERGED - Hip Spindle.stl
GeoMagic/Version 0.3 - Abandoned/STL Files/SCALE_MIRROR ON FRM A - Frame B.stl
GeoMagic/Version 0.3 - Abandoned/STL Files/MERGED - Hip Arm L.stl
GeoMagic/Version 0.3 - Abandoned/STL Files/MERGED - Hip Arm R.stl
GeoMagic/Parts/Belt Gears/615376.STEP
GeoMagic/Parts/Belt Gears/615378.STEP
GeoMagic/Parts/Belt Gears/615384.STEP
GeoMagic/Parts/Belt Gears/615386.STEP
GeoMagic/Version 0.3 - Abandoned/STL Files/Frame Inner Collar.stl
GeoMagic/Version 0.3 - Abandoned/STL Files/MERGED - Thigh Arm L.stl
GeoMagic/Version 0.3 - Abandoned/STL Files/MERGED - Thigh Limb.stl
GeoMagic/Version 0.3 - Abandoned/STL Files/Nut - Pot-Mini.stl

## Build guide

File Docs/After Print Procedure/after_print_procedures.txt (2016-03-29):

==============================
AFTER PRINT CLEANUP PROCEDURES
==============================

******  FRAME ******

  BEFORE CURING
  -------------

    - Remove problematic print support leftovers
        - clean up all bearing seats
        - clean up pot seating surfaces
       
    - Use paperclip to clear all arm stopper holes

  AFTER CURING
  ------------

    - remove burrs with nail salon sander
      - sand edges 
      - sand motor seating surface

****** SPINDLE ARM ******

  BEFORE CURING
  -------------

    - Remove problematic print support leftovers
        - clean up cable clamp holes and wire exits

    - Use paperclip to make sure retain hold goes all the way through

  AFTER CURING
  ------------

    - remove burrs with nail salon sander
      - sand edges 

****** FRAME SPINDLE ******

  BEFORE CURING
  -------------

    - Remove problematic print support leftovers
      - clean up bearing seats
      - make sure round shaft has no bumps
      - make sure no burrs on hexagonal parts

    - Use paperclip to make sure both retaining
      pin holes go all the way through

  AFTER CURING
  ------------

    - remove burrs with nail salon sander

    - dry fit to frame, bearings, spindle arm and hip limb
      and sand if neceesary

--------------------------------------------------
------------------ TEMPLATE ----------------------
--------------------------------------------------

****** PART ******

  BEFORE CURING
  -------------

    - Remove problematic print support leftovers

    - Use paperclip to 

  AFTER CURING
  ------------

    - remove burrs with nail salon sander
      - sand edges

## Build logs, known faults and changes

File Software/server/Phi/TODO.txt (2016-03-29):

TO DO LIST
==========

#
# PHI SERVER
#

* Implement JSON calling routines.

* Implement better connectivity - see description in firmaware

* Change action factory methods to classes ... it's nicer

* Think about what a reasonable frame rate is.  Think of the speed of joints
  in ADC units and what kind of angle resolution one might expect given
  a particular tolerance, timeout, etc.

* Joint position tolerance should be a parameter because different values
  are achievable at different speeds.

* Write some sort of MoveAction that takes speed into account.  Should ramp
  up?  Allow specification of max power?  Or is adaptive seek enough?

* Adaptive seek logs require non-circular buffers.  Implement.

* Set up some sort of DEBUG flag bit field with checked menu to enable.

* There's some sort of bug where the "activeLog == NULL" assertion fails.

* Also think about what can happen if there's a forever action and we add another.
  Are lists being duplicated everywhere they should to prevent changes?

#
# PHI FIRMWARE
#

* HW pumps need to run at a rate adequate to the frame rate. Add new param 
  to JSON start phi link command for server to communicate expected frame rate.
  Use this to set pump delay.

* Performance web page does not correctly report UART expected loop period.  This is
  because it now runs off of an event.  Change it to report expected frame period.

* Check motor controller initialization - last time I looked, it was not in an ideal mode.

* Improve PhiLink connectivity.

	1) When Phi starts up, it sets serverIP to zero and starts the PhiLink thread immediately.
	   While serverIP is zero, the thread goes into an infinite loop sending out a UDP broadcast
	   beacon every second or so.

	2) The server is listening for the beacon and when it receives it, it determines Phi's IP address
	   from the packet and calls a new JSON setServerIP call to pass the server's IP to Phi.  Upon
	   return from the JSON call, the server closes its beacon listening port and opens its PhiLink
	   listening port.

	4) When Phi receives the setServerIP call, it sets the serverIP variable, releasing the PhiLink thread
	   from its infinite loop that sends the UDP beacon packets.  The thread now connects to the server
	   and starts its comm loop.

	5) When the server exits, Phi gets an error.  This should make the comm loop fall back to
	   beacon mode.

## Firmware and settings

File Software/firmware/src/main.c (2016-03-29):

//
// spiderBot entry point
//

// create globals here
#define GLOBAL_INIT

#include "phi.h"

// uncomment to debug mem allocations
//
// You must also do:
//      "export MALLOC_TRACE=mtrace.out" in shell
//      cd bin
//      sudo ../bin-debug/phi-ubuntu
//
// #include <mcheck.h>
// #define PHI_DEBUG_MALLOC    1

void main(int argc, char** argv) {

  // initialize
  globalInit();

  // process command line switches
  cmdline(argc, argv);

  // start the hardware pump threads now that we survived
  // the cmdline processing.  The cmdline processing can exit
  // on errors and when being used to create a test suite script.
  startHwPump();

  //
  // Start web admin server
  //
  // Note: the main thread is dedicated to the admin web server
  // main loop.
  //
  
  webAdmin(80, "./wwwRoot");

  // never gets here
  LOG_FATAL("webAdmin returned!");
  
}

//
// Global intialization
//

void globalInit() {
  
  #ifdef PHI_DEBUG_MALLOC
    mtrace();
  #endif

  // remember start-up time
  struct timeval tv;
  gettimeofday(&tv, NULL);
  g_startupTime = TV_TO_USEC(tv);

  // startup message (in case log will fail)
  time_t now = time(NULL);
  char* sTime = ctime(&now);
  printf("PHI started at %s", sTime);

  // get system info
  if (uname(&g_uname) < 0) {
    LOG_FATAL("could not get system info - uname() failed");
  }

  // get IP of (probable) interface we will get requests from
  g_ipAddr = getHostIP();

  // init log
  if (logInit(LOGFILE_NAME) == 0) {
    // failed
    LOG_FATAL("Error: could not open log file '%s' (errno=%d)!  (Are you running as root?)\n", LOGFILE_NAME, errno);
  }

  // remove NL and log
  sTime[strlen(sTime)-1] = 0;
  
  LOG_INFO("");
  LOG_INFO("#######");
  LOG_INFO("####### PHI startup at %s #######", sTime);
  LOG_INFO("#######");
  LOG_INFO("");

  // initialize HAL
  HAL_init();

  //
  // Init performance logs
  //

  // phiLink
  g_pDlog_phiLink_period        = dlog_create("PhiLink Period", "uS", PERFLOG_PHILINK_NUM_ELEM, PERFLOG_PHILINK_EPOCH);  

  // pump period
  g_pDlog_hwPump_UART_period    = dlog_create("UART Period", "uS", PERFLOG_HWPUMP_NUM_ELEM, PERFLOG_HWPUMP_EPOCH);  
  g_pDlog_hwPump_SPI_period     = dlog_create("SPI Period",  "uS", PERFLOG_HWPUMP_NUM_ELEM, PERFLOG_HWPUMP_EPOCH);
  g_pDlog_hwPump_I2C_period     = dlog_create("I2C Period",  "uS", PERFLOG_HWPUMP_NUM_ELEM, PERFLOG_HWPUMP_EPOCH);

  // pump work duration
  g_pDlog_hwPump_UART_workTime  = dlog_create("UART Work Dur", "uS", PERFLOG_HWPUMP_NUM_ELEM, PERFLOG_HWPUMP_EPOCH);
  g_pDlog_hwPump_SPI_workTime   = dlog_create("SPI Work Dur",  "uS", PERFLOG_HWPUMP_NUM_ELEM, PERFLOG_HWPUMP_EPOCH);
  g_pDlog_hwPump_I2C_workTime   = dlog_create("I2C Work Dur",  "uS", PERFLOG_HWPUMP_NUM_ELEM, PERFLOG_HWPUMP_EPOCH);

  //
  // Init peripherals
  //
  
  char* p = HAL_initPeripherals();

  if (p != NULL) {
    LOG_FATAL("Peripherals did not initialize.\n%s", p);
  } else {
    LOG_INFO("Peripherals initialized");
  }
}

//
// Shutdown
//

void globalShutdown() {

  LOG_INFO("*** Shutting down hardware ***");

  // stop motors
  stopAllMotors();
}

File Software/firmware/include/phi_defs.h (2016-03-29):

//
// spiderBot common types
//

#define PHI_VERSION     "0.1 dev"

//
// GENERIC DEFS
//
// Note: use GNU types to make sure things are what
// we expect.
//

// signed ints
#define INT8            int8_t
#define INT16           int16_t
#define INT32           int32_t
#define INT64           int64_t

// unsigned ints
#define UINT8           uint8_t
#define UINT16          uint16_t
#define UINT32          uint32_t
#define UINT64          uint64_t


// common data aliases

#define BYTE            UINT8
#define WORD            UINT16
#define DWORD           UINT32
#define BOOL            UINT8

#define FALSE           0
#define TRUE            1

// math macros
#define COUNTOF(arr)    ((int) (sizeof(arr) / sizeof(arr[0])) )
#define MIN(a,b)        ( ((a) < (b)) ? (a) : (b) )
#define MAX(a,b)        ( ((a) > (b)) ? (a) : (b) )

// allocation helpers

#undef  ALLOC           // prevent confusion
#undef  FREE
#undef  ZERO
#undef  ZERO_P

#define PHI_ALLOC(D)    ((D*)allocHelper(sizeof(D)))
#define PHI_ALLOC_N(n)  allocHelper(n)
#define PHI_FREE(p)     {free(p); p = NULL; }

#define PHI_ZERO(v)     memset(&(v), 0, sizeof(v))
#define PHI_ZERO_P(p,l) memset(p, 0, l)

// preprocessor

#define BASH_BLACK      "30"
#define BASH_RED        "31"
#define BASH_GREEN      "32"
#define BASH_YELLOW     "33"
#define BASH_BLUE       "34"
#define BASH_MAGENTA    "35"
#define BASH_CYAN       "36"
#define BASH_WHITE      "37"

#define BASH_START_COLOR(c)   "\e[1;" c "m"
#define BASH_STOP_COLOR       "\e[0m"

#define DO_PRAGMA(x)    _Pragma (#x)
#define INFO(m)         DO_PRAGMA(message (BASH_START_COLOR(BASH_GREEN)  "INFO - " m BASH_STOP_COLOR))
#define TODO(m)         DO_PRAGMA(message (BASH_START_COLOR(BASH_CYAN)  "TODO - " m BASH_STOP_COLOR))
#define WARN(m)         DO_PRAGMA(message (BASH_START_COLOR(BASH_YELLOW)    "WARNING - " m BASH_STOP_COLOR))
#define HACK(m)         DO_PRAGMA(message (BASH_START_COLOR(BASH_RED) "HACK - " m BASH_STOP_COLOR))

// time
#define U64_1E6         ((UINT64)1e6)
#define TV_TO_USEC(tv)  ( (((UINT64)tv.tv_sec) * U64_1E6) + ((UINT64)tv.tv_usec) )

// logging
#define LOG_INFO(...)   logMsg("", __VA_ARGS__)
#define LOG_ERR(...)    logMsg("ERROR: ", __VA_ARGS__)
#define LOG_FATAL(...)  { printf("FATAL: "); printf(__VA_ARGS__); printf("\n"); logMsg("FATAL: ", __VA_ARGS__); abortProcess(-1); }

// stringifying helpers
#define STR(s)                #s              /* convert to string */
#define STR_MACRO(m)          STR(m)          /* convert to string (version for use inside a macro - requires two steps */
#define Q(s)                  "\"" #s "\""    /* convert to quoted string */

//
// PHI SPECIFIC DEFS
//

// logging
#define LOGFILE_NAME    "/var/log/phi.log"

#define LOG_LEVEL                 (LOG_LEVEL_HTTP | LOG_LEVEL_JSON)
#define LOG_LEVEL_HTTP            0x0001
#define LOG_LEVEL_HTTP_VERBOSE    0x0002
#define LOG_LEVEL_JSON            0x0004
#define LOG_LEVEL_JSON_VERBOSE    0x0008

// HTTP/JSON buffers
#define HTTP_BUFFSIZE       (16*1024)      // max size of HTTP request/reply
#define JSON_TMP_BUFFSIZE   (4*1024)       // max size of single JSON reply

// Linux drivers
#define UART_DRIVER_NAME  "/dev/ttyAMA0"
#define SPI0_DRIVER_NAME  "/dev/spidev0.0"
#define SPI1_DRIVER_NAME  "/dev/spidev0.1"

// LED colors

typedef enum {
    OFF,
    RED,
    FLASH_RED,
    YELLOW,
    FLASH_YELLOW,
    GREEN,
    FLASH_GREEN
    
} PHI_LED_COLOR;

// cam info (move to cam file when it exists)
#define CAM_WIDTH               8 //160
#define CAM_HEIGHT              8 // 120
#define CAM_NUM_BYTES           (CAM_WIDTH * CAM_HEIGHT)

// PhiLink
#define DEF_PHILINK_PORT  1122

// SPI indexes
#define GYRO_SPI_IDX      0         // gyro at idx 0
#define ADC_SPI_IDX       1         // ADCs at idx 1

// mutex macros

#define PHI_MUTEX_VAR_TYPE          pthread_mutex_t
#define PHI_MUTEX_INITVAL           PTHREAD_MUTEX_INITIALIZER
#define PHI_MUTEX_DECL(name)        PHI_MUTEX_VAR_TYPE name
#define PHI_MUTEX_DECL_INIT(name)   PHI_MUTEX_DECL(name) = PHI_MUTEX_INITVAL
#define PHI_MUTEX_INIT(pMtx)        pthread_mutex_init(pMtx, NULL)
#define PHI_MUTEX_GET(pMtx)         pthread_mutex_lock(pMtx)
#define PHI_MUTEX_RELEASE(pMtx)     pthread_mutex_unlock(pMtx)
#define PHI_MUTEX_TRYGET(pMtx)      pthread_mutex_trylock(pMtx)   // ret 0 if get successful, ret != if failed

// hardware pumping rate
#define HWPUMP_LOOPS_PER_SEC        30
#define HW_PUMP_LOOP_PERIOD_USEC    ((INT32)(1e6 / HWPUMP_LOOPS_PER_SEC))

// performance monitoring

#define PERFLOG_HWPUMP_ELEM_1SEC      HWPUMP_LOOPS_PER_SEC
#define PERFLOG_HWPUMP_ELEM_5SEC      (5 * PERFLOG_HWPUMP_ELEM_1SEC)
#define PERFLOG_HWPUMP_ELEM_15SEC     (15 * PERFLOG_HWPUMP_ELEM_1SEC)
#define PERFLOG_HWPUMP_NUM_ELEM       PERFLOG_HWPUMP_ELEM_15SEC
#define PERFLOG_HWPUMP_EPOCH          15
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

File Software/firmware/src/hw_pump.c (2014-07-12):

//
// Hardware pump threads
//
// Create separate threads responsible for:
//
// 1) Pumping data from all devices and updating a snapshot of the current state.
// 2) Heartbeat on status LED
// 3) Failsafe checking for conditions that might damage the robot
// 

#include "phi.h"

//
// DEFINES
//

//
// VARS
//

// snapshot of phi (cmds and sensor states)

typedef struct {

  PHI_CMD_PACKET cmds;
  PHI_STATE_PACKET state;

} PHI_SNAPSHOT;

static PHI_SNAPSHOT phiSnapshot;

// mutex to sync access to phiSnapshot
static PHI_MUTEX_DECL_INIT(mtxSnapshot);

// event gates
static PHI_EVENT_GATE egMotorWrite;;

// debug count of egMotorWrite timeouts
static DWORD numMotorTimeouts = 0;

//
// PROTOS
//

void initSnapshot();

void* hwPump_UART_thread(void* arg);
void* hwPump_SPI_thread(void* arg);
void* hwPump_I2C_thread(void* arg);

//
// CODE
//

/*

  The main purpose of startHwPump is to start helper threads to continually and efficiently keep synchronized the true
  hardware state and its snapshot in phiSnapshot.  This involves continually polling the hardware and updating phiSnapshot.

  To be efficient, we must take into account that:

  1) We have three different interfaces to poll so they can be done in parallel (UART, SPI and I2C). For simplicity,
     we start a separate "pump" thread for each interface.
  
  2) Access to phiSnapshot must also be synchronized between threads.
  
*/

void startHwPump() {

  // DEBUG
  //
  // WARN("pump disabled");
  // printf("*** Hw pump disabled ***\n");
  // return;

  // init phi snapshot
  initSnapshot();

  // init the event gate that synchronizes writing out to the motors (init to CLOSED)
  eventGate_init(&egMotorWrite, FALSE);
  
  // spawn threads to pump each interface
  //
  // Note: threads are started detached and we don't keep track
  // of the pthread_t, threads are "fire and forget"

  int iface;

  for (iface = 0 ; iface < 3 ; iface++) {

    pthread_t thread;
    pthread_attr_t threadAttr;

    // init default attrs
    PHI_ZERO(threadAttr);
    pthread_attr_init(&threadAttr);

    // request detached thread
    pthread_attr_setdetachstate(&threadAttr, PTHREAD_CREATE_DETACHED);

    /* NO ARGUMENTS 
    // alloc args
    PHILINK_ARGS* pArgs = PHI_ALLOC(....);
    pArgs -> a = a;
    pArgs -> b = b;
    */

    // create interface thread

    switch(iface) {
      case 0:
        pthread_create(&thread, &threadAttr,  &hwPump_UART_thread, NULL);
        break;
      case 1:
        pthread_create(&thread, &threadAttr,  &hwPump_SPI_thread, NULL);
        break;
      case 2:
        pthread_create(&thread, &threadAttr,  &hwPump_I2C_thread, NULL);
        break;
    }

    // release thread attr because we don't use it
    pthread_attr_destroy(&threadAttr);

    // increase priority to make pumps more even
// Note: not sure if this is a good idea
//
//    if (setRealtimePrio(thread) == FALSE) {
//      // not fatal
//      LOG_ERR("pump set_realtime_priority() failed!");
//    }
    
  } // for
  
}

/////////////////////////////////////////////////
//
// UART pump thread
//
// Devices serviced by UART:
//
//     motor controllers (TX only)
//
/////////////////////////////////////////////////

static UINT64 UART_loopStart_save = 0;

void* hwPump_UART_thread(void* arg)
{
  LOG_INFO("hwPump_UART_thread started");
  printf("UART pump thread started\n");

  // update motor controllers from snapshot whenever we
  // are told to do it by egMotorWrite being pulsed.
  //
  // note: if the event gate times out, the motors are set to coast
  //       to prevent damage.
  //

  // time at start of loop
  UINT64 usec_loopStart = phiUpTime();

  while (TRUE) {

    int ctrlID;
    int selIdx;
    int motorIdx = 0;

    //
    // Send motor power commands to all controllers
    //

    // go through each controller
    for (ctrlID = 0 ; ctrlID <= 5 ; ctrlID ++) {
      // go through each motor of this controller
      for (selIdx = 0 ; selIdx <= 1 ; selIdx ++) {
        // send out motor power command for this motor

        lock_snapshot();
        float power = phiSnapshot.cmds.motors[motorIdx++];
        unlock_snapshot();

        // snapshot power is [-1, 1], convert to [0, 127], bFwd
        BYTE absPower = (BYTE) (fabs(power) * 127);
        BOOL bFwd = (power >= 0) ? TRUE : FALSE;
        
        HAL_setMotorPower(ctrlID, selIdx, absPower, bFwd);
      }
    }

    // time at end of work
    UINT64 usec_workEnd = phiUpTime();
    INT32 usec_workTime = (INT32) (usec_workEnd - usec_loopStart);

    //
    // Wait on event gate to be told data has been updated
    //
    // The purpose of the event gate is to allow commands to be written to the
    // UARTs as quickly as possible after they are received.  It is basically an
    // interruptible sleep. We wait on the gate but timeout if it takes too long.
    // When a timeout occurs, it means we have not received commands from the
    // server for a while and something is seriously wrong.  In this case, we
    // stop all motors for safety.

    #define MOTOR_TIMEOUT_MS   500      // 1/2 second

    int waitRc = eventGate_wait(&egMotorWrite, MOTOR_TIMEOUT_MS);

    if (waitRc == ETIMEDOUT) {

      // gate timed out - only bad if link connected

      if (g_phiLinkStatus == LINK_CONNECTED) {

        // link is connected - stop all motors
        stopAllMotors();

        // count it
        numMotorTimeouts ++;

        // DEBUG
        LOG_INFO("eventGate timeout in UART pump - count=%lu", numMotorTimeouts);
      }
    }
        
    // new loop start
    usec_loopStart = phiUpTime();

    // log loop period
    
    if (UART_loopStart_save != 0) {
      dlog_addElem(g_pDlog_hwPump_UART_period, usec_loopStart-UART_loopStart_save);
    }
    
    UART_loopStart_save = usec_loopStart;

    // log loop work time
    dlog_addElem(g_pDlog_hwPump_UART_workTime, usec_workTime);
    
    
  } // while
  
} // hwPump_UART_thread

/////////////////////////////////////////////////
//
// SPI pump thread
//
// Devices serviced by SPI:
//
//     Gyro (SPI index 0)
//     ADCs (SPI index 1)
//
/////////////////////////////////////////////////

static UINT64 SPI_loopStart_save = 0;
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

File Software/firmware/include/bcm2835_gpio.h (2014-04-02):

//
// Helpful file from git project
//
// Full at: Spider-Droid/Software/third-party/RaspberryPi-GPIO
//
// To retrieve: clone https://github.com/alanbarr/RaspberryPi-GPIO.git
//

/**
 * @file
 *  @brief Header file for BCM2835 GPIO registers.
 *
 *  This is is part of https://github.com/alanbarr/RaspberryPi-GPIO
 *  a C library for basic control of the Raspberry Pi's GPIO pins.
 *  Copyright (C) Alan Barr 2012
 *
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
 *  The addresses of the GPIO registers are the physical addresses of the GPIO
 *  registers as available through /dev/mem.
 *  From page 6 of BCM2835 ARM Peripherals:
 *      Physical addresses range from 0x20000000 to 0x20FFFFFF for peripherals.
 *      The bus addresses for peripherals are set up to map onto the peripheral
 *      bus address range starting at 0x7E000000.
 *      Thus a peripheral advertised here at bus address 0x7Ennnnnn is available
 *      at physical address 0x20nnnnnn.
*/

#ifndef _BCM_2835_
#define _BCM_2835_

/******************************************************************************/
/* The following are the physical GPIO addresses                              */
/******************************************************************************/
#define GPFSEL0                 0x20200000  /**<GPIO Function Select 0 Register Address */
#define GPFSEL1                 0x20200004  /**<GPIO Function Select 1 Register Address */
#define GPFSEL2                 0x20200008  /**<GPIO Function Select 2 Register Address */
#define GPFSEL3                 0x2020000C  /**<GPIO Function Select 3 Register Address */
#define GPFSEL4                 0x20200010  /**<GPIO Function Select 4 Register Address */
#define GPFSEL5                 0x20200014  /**<GPIO Function Select 5 Register Address */

#define GPSET0                  0x2020001C  /**<GPIO Pin Output Set 0 Register Address */
#define GPSET1                  0x20200020  /**<GPIO Pin Output Set 1 Register Address */

#define GPCLR0                  0x20200028  /**<GPIO Pin Output Clear 0 Register Address */
#define GPCLR1                  0x2020002C  /**<GPIO Pin Output Clear 1 Register Address */

#define GPLEV0                  0x20200034  /**<GPIO Pin Level 0 Register Address */
#define GPLEV1                  0x20200038  /**<GPIO Pin Level 1 Register Address */

#define GPEDS0                  0x20200040  /**<GPIO Pin Event Detect Status 0 Register Address */
#define GPEDS1                  0x20200044  /**<GPIO Pin Event Detect Status 1 Register Address */

#define GPREN0                  0x2020004C  /**<GPIO Pin Rising Edge Detect Enable 0 Register Address */
#define GPREN1                  0x20200050  /**<GPIO Pin Rising Edge Detect Enable 1 Register Address */

#define GPHEN0                  0x20200064  /**<GPIO Pin High Detect Enable 0 Register Address */
#define GPHEN1                  0x20200068  /**<GPIO Pin High Detect Enable 1 Register Address */

#define GPAREN0                 0x2020007C  /**<GPIO Pin Async. Rising Edge Detect 0 Register Address */
#define GPAREN1                 0x20200080  /**<GPIO Pin Async. Rising Edge Detect 1 Register Address */

#define GPAFEN0                 0x20200088  /**<GPIO Pin Async. Falling Edge Detect 0 Register Address */
#define GPAFEN1                 0x2020008C  /**<GPIO Pin Async. Falling Edge Detect 1 Register Address */

#define GPPUD                   0x20200094  /**<GPIO Pin Pull-up/down Enable Register Address */

#define GPPUDCLK0               0x20200098  /**<GPIO Pin Pull-up/down Enable Clock 0 Register Address */
#define GPPUDCLK1               0x2020009C  /**<GPIO Pin Pull-up/down Enable Clock 1 Register Address */


/**********************************************************************************/
/* The following are offset address which can be used with a pointer to GPIO_BASE */
/**********************************************************************************/
#define GPIO_BASE               GPFSEL0   /**< First GPIO address of interest. */

#define GPFSEL0_OFFSET          0x000000  /**< GPIO Function Select 0 Offset from GPIO_BASE */
#define GPFSEL1_OFFSET          0x000004  /**< GPIO Function Select 1 Offset from GPIO_BASE */
#define GPFSEL2_OFFSET          0x000008  /**< GPIO Function Select 2 Offset from GPIO_BASE */
#define GPFSEL3_OFFSET          0x00000C  /**< GPIO Function Select 3 Offset from GPIO_BASE */
#define GPFSEL4_OFFSET          0x000010  /**< GPIO Function Select 4 Offset from GPIO_BASE */
#define GPFSEL5_OFFSET          0x000014  /**< GPIO Function Select 5 Offset from GPIO_BASE */

#define GPSET0_OFFSET           0x00001C  /**< GPIO Pin Output Set 0 Offset from GPIO_BASE */
#define GPSET1_OFFSET           0x000020  /**< GPIO Pin Output Set 1 Offset from GPIO_BASE */

#define GPCLR0_OFFSET           0x000028  /**< GPIO Pin Output Clear 0 Offset from GPIO_BASE */
#define GPCLR1_OFFSET           0x00002C  /**< GPIO Pin Output Clear 1 Offset from GPIO_BASE */
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

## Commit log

2013-07-13 spawn threads to handle HTTP requests
2013-07-18 JSON request framework complete
2013-07-20 temp debug motor test
2013-07-21 added debug button to web admin
2013-07-21 hack until controller IDs set up correctly
    [motor.c]
2013-07-21 until motor init sets 8-bit speed
2013-07-23 added prelim SPI code
2013-07-23 added spi.c and plax_L3G4200D.h
2013-07-24 mods to gyro setup
2013-07-24 RPi SPI test tool
2013-07-24 Added schematics
    [Phi.sch]
2013-07-26 modified SPI api, renamed UART SPI
2013-07-26 changed gyro to MSB first because SPI driver was failing open()
    [plax_L3G4200D.h]
2013-07-26 added comments to explain MSB + little-endian requirement for gyro
2013-07-26 wired up JSON gyro calls
2013-07-26 take gyro out of power-down mode on startup - duh ...
2013-07-26 fixed log msg that prints JSON request keywords
    [webjson.c]
2013-07-27 reorganized web pages ; fixed mem corruption in webjson.c ; added gyro dials
    [main.c, webjson.c]
2013-07-27 tweaked gyroscope page
2013-08-05 chkpt: phiLink gyro code
2013-08-05 schematics + minor phi link changes
2013-08-05 phi schematics
    [Phi.sch]
2013-08-07 removed init peripherals button since it happens automatically now
2013-08-07 enable FIFO in stream mode in gyroscope
2013-08-07 fixed bug in gyro code
    [gyro.c]
2013-08-08 no longer return gyro info in DPS, now return deltas
    [gyro.c, hal.c, webjson.c]
2013-08-08 filter out spurious rpi-phi messages
2013-08-09 changed code that reads gyro FIFO
2013-08-09 fixed casting bug in gyro FIFO code
    [gyro.c]
2013-08-09 added calibration and thresholding to gyro code
2013-08-10 added support for second SPI port and full-duplex SPI
2013-08-14 chkpt: Added controls for most sensors
2013-08-17 chkpt: ADC read code
2013-08-17 debug code in ADC code ; failsafe function added - not wired in yet
    [motor.c]
2013-08-17 added failsafe file - not wired in yet
2013-08-18 fixed SPI code to properly use the right file descriptor
    [mcp3008.h, spi.c, uart.c]
2013-08-19 fixed stupid bug in getMotorPosition ... sigh
    [motor.c]
2013-08-31 added failsafe thread
2013-08-31 removed debug code from motor code
2013-09-04 made rx/tx buffers static in case stack space is small
2013-09-09 gyro accum on phi to fix loss issue
    [gyro.c]
2013-09-11 tweak motor slider control to prevent swamping PHI
2013-09-25 checkpoint before redesign of motor mount / pulleys
    [Spider Globals.csv]
2013-09-30 Added GeoMagic directory since Alibre changed its name
    [Spider Globals.csv]
2013-10-01 checkpoint: refactor CAD files
2013-10-06 added new screws
2013-10-06 don't hold semaphore during serial/SPI comms
2013-10-06 added max power to diag page
2013-12-04 added set motor controller ID code
2013-12-04 placeholder for accelerometer files
2013-12-26 reorg + created Gyro and Accel
2014-01-08 Checkpoint - Heavy changes in plastic
    [Torque.xlsx]
2014-01-22 modified motor control functions to use simpler names, added datalog.c and cubic.c, minor tweaks
2014-01-22 deepened grooves ; changed pulley hole to slot for easier assy ; added air vent for assy ; changed wire attach mechanism to fit crimp
2014-01-29 chkpt - worked on pump threads
2014-02-05 file to keep track of random thoughts
2014-02-21 changed case of some include files
2014-03-01 added placeholder for I2C init and accel init
2014-03-01 fixed bug that effectively disabled uart_send()
    [uart.c]
2014-03-01 fixed minor bug in HAL_setMotorPower()
    [webjson.c]
2014-03-02 added macros for converting temperature to canonical [0,1] range
2014-03-02 only start hw pumps after connected + minor cleanup
2014-03-02 reenabled hw pumps, cleaned up loops to make simpler, still need to deal with new canonical values
2014-03-02 use new motor names
2014-03-02 change phi_setPower() to use new motor names
2014-04-01 changed colors for better visualization ; moved lock pin holes
2014-04-01 smaller clearance in pot stops; hacky shim on shins pot mount to clear wires
2014-04-02 added GPIO support ; SPI 1 multiplex w GPIO CS
2014-04-05 chkpt: wired event gate
2014-07-04 fixed bug in event gates, tweaked UART event loop, now activate hw pumps immediately
    [hw_pump.c, main.c, phi_defs.h]
2014-07-04 added switch to warn about undecl funcs ; JSON now interacts with snapshots to send motor cmds
2014-07-04 fixed weird default UNSIGNED chars! Really?git status?
    [hw_pump.c, motor.c, phi_defs.h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]
2014-07-05 wire threader
2014-07-11 converted all doubles to floats because they are smaller and faster on ARM
2014-08-06 Added PhiAction framework
2014-09-03 added Stand Adapter and mods to wire tie on Shin and Hip Rocker
2015-05-14 Moved a ton of stuff around because gave up on previous scheme of driving legs because the kevlar strings always break.
    Tried an intermediate version that didn't pan out because of
    excessive friction
    Now trying version 0.3 of plastic
    [Spider Globals.csv]
2015-05-14 Misc changes for v 0.3
    [615376.STEP, 615378.STEP, 615384.STEP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]
2016-04-08 Commit all in prep to switch to BitBucket

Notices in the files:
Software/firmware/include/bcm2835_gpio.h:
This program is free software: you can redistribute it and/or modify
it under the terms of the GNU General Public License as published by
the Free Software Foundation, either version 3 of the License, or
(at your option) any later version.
